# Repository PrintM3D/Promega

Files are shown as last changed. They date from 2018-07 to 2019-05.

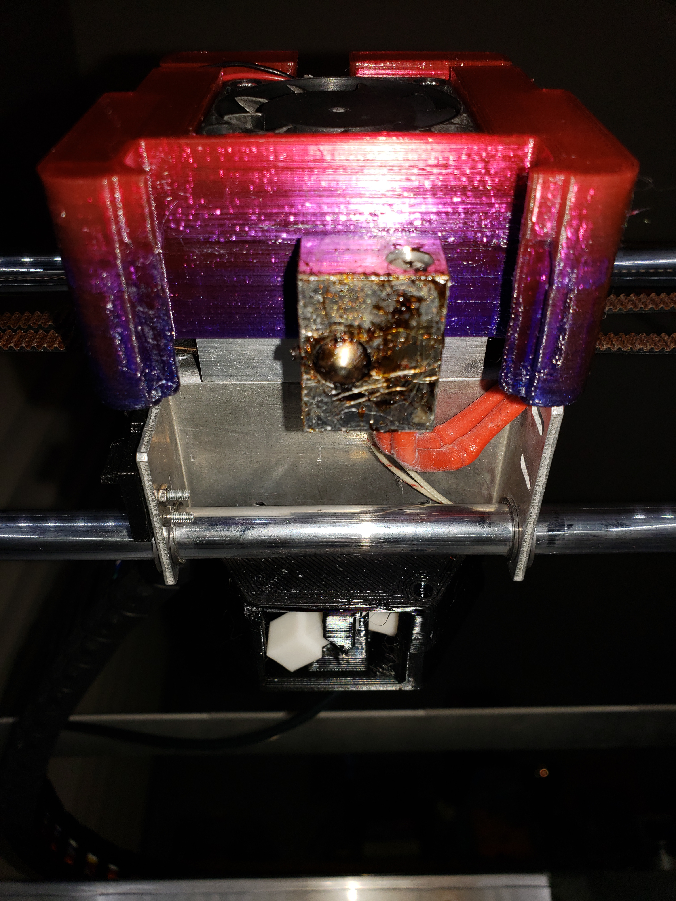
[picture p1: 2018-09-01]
addons/ShadowHawk/Fan Shroud/Photos/20180901_033425.jpg

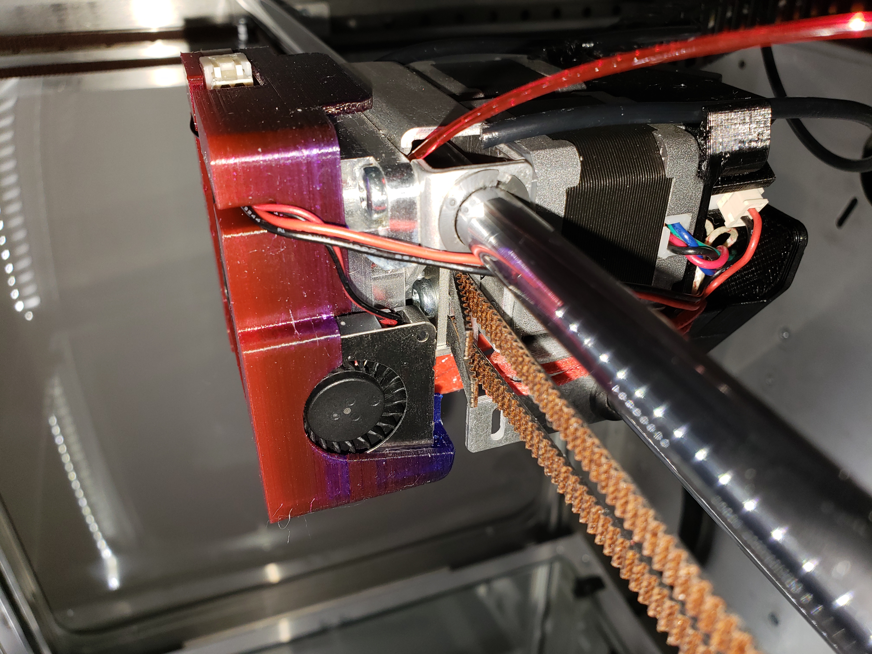
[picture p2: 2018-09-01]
addons/ShadowHawk/Fan Shroud/Photos/20180901_033406.jpg

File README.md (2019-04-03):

## Promega

> A curated repo of the official settings and files for the Promega 3D Printer.

## This Repository

* [Slicer_Profiles](https://github.com/PrintM3D/Promega/tree/devel/Slicer_Profiles) - Promega Slicer Profiles
* [SD Card Structure](https://github.com/PrintM3D/Promega/tree/devel/SD%20Card%20Structure) - Official SD folder releases

## Links
* [Promega Docs](http://promega.printm3d.com) - Official Promega Documentation. 

## Addons
* [Addons](https://github.com/PrintM3D/Promega/tree/devel/addons) - Collection of addons created by M3D and the community.

## Instructions Links:
* [How to Download SD Card Content](https://promega.printm3d.com/getting-started/updating-sd-card-structure)

## Creating Issues 
Please log ONLY issues pertinent to software bugs or operational anomalies (suspected to be software-related).
Any other type of issues logged will be not be addressed and will be deleted.

If you are looking for support, feel free to look through our ever-improving documentation for quick help. 

- [M3D's Official Troubleshooting & Self-Help Guide](https://coda.io/d/M3D-Official-Troubleshooting-Self-Help-Guide_dzE73kMbIAL/Introduction_sucuq#_lulpw)
- [Promega Guides & Instructions](https://promega.printm3d.com/)

If you'd like to voice your input on improving our documentation, visit: 
- M3D's Official Troubleshooting & Self-Help Guide [Contribution & Suggestion Page](https://coda.io/d/M3D-Official-Troubleshooting-Self-Help-Guide_dzE73kMbIAL/Coda-Edits-Requests-Form_suKF6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)
- Promega Guides & Instructions [Contribution & Suggestion Page](https://promega.printm3d.com/#contributing)

Our support ticket is available at https://store.printm3d.com/pages/support.

-M3D Team

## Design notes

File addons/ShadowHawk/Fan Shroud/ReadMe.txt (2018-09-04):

This is a 3D printable fan shroud for the ProMega using the original front and part fans.
It can also accommodate a Noctua 40x40x12 fan.

Please note, to install this fan shroud, you have to turn your heat block by 90 degrees with the wires coming out the back.  Please refer to the photos on how the cables should be routed.

The cable for the part fan needs to be removed from the front cable assembly.  You then have to pull a bit more of the cable through the cable chain (there is plenty of slack at the board end).  Refer to the photos on how the part fan cable should be routed and how the plug fits into the fan shroud.

This was modeled in Fusion 360 and I included the Fusion 360 archive file in the CAD folder together with just about any other format Fusion 360 can export.  The STL is in the folder STL (shocking).  The Simplify3D folder has a factory file in it.  The speed is set to 30mm/s, please adjust to what ever your printer is capable of printing.
The GCode folder has two files in it.  One is using Tool 0, the other one is modified to use the mixing tool with a linear gradient between the right and the left extruder.

This version now fits under the front metal edge.  You will need to adjust your Max Y in machine_axisdimension.g from 388 down to 372 due to the radius at the front of the case, BUT, you gain some cooling for your extruder steppers in return.

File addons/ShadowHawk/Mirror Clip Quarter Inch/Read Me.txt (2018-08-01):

In my setup I'm using a custom cut 16 3/8" x 16 3/8" x 1/4" mirror with half inch radius corners.
The mirror ended up being 5.99mm thick which is too thick for the regular bed clips.

I designed these clips to go between the bedframe and the heat bed and hold the mirror in place on top.
The mirror is pretty heavy as it is so this is really just a little bit of additional piece of mind.

I printed the clips in Black Inland PETG with 0.5mm nozzle, 0.25mm layer height and 30mm/s speed.

Simplify3D factory provided for convenience

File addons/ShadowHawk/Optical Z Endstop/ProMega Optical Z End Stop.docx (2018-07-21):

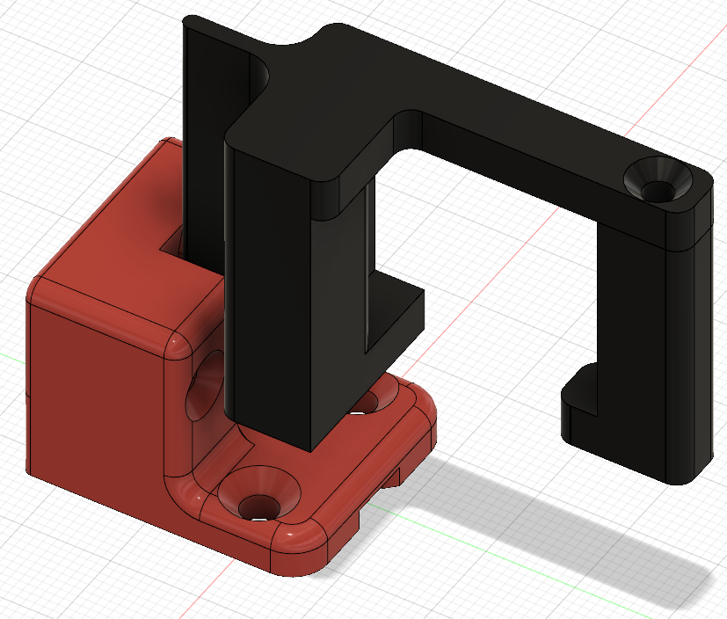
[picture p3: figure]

# ProMega Optical Z End Stop

# Introduction

In a CoreXY printer setup, the Z end stop is usually located at the bottom of the printer which equates to the maximum Z extent. Due to this, having an accurate and repeatable height measurement from that end stop to the nozzle is very important. In the existing Z end stop design, the bed rests on the actual mechanical switch and the switch is not mechanically fixed in the Z direction, i.e. it can have a little bit of play. Even if the amount of possible Z movement of the switch is only 0.5mm, that is by far too much, causing issues with repeatable Z zero position after homing the Z axis.

The Optical Z End Stop design solves those issues and yields perfect Z zero position every time.

# Bill of Materials

The following parts are needed:

- Optical Switch, here are two links, they are all the same model, just different quantities. This should give you an idea of the model used. There are other optical switches but they might not fit the 3D printed case below. https://www.amazon.com/Solu-Optical-Endstop-Printer-Makerbot/dp/B00V2QPU4M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 https://www.amazon.com/HONG111-Optical-Endstop-Control-Printer/dp/B071KBC3P8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
- 3D Printed Optical End Stop Housing Optical Z Endstop Holder.stl
- 3D Printed Slider Fin Main Fin.stl
- 3D Printed Counter Mount Counter Mount.stl
- 3 x M3 x 12mm countersunk screw
- 2 x M3 nut
- 2 x Small Cable Tie
- 1 Dupont 3 port plug (optional) https://www.amazon.com/620-PCS-2-54mm-Pitch-JST/dp/B07BCYTL7R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
- 1 M3 Threaded Brass Insert (something like the link below) https://www.amazon.com/a16041800ux0827-Cylindrical-Knurled-Threaded-Embedded/dp/B01IZ1RN0A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

# Assembly

## Optical End Stop

Make sure that the optical switch is perfectly flat against the PCB. If necessary, heat the pins up with a soldering iron and press the switch on the PCB until it is flat. Pay attention not to ruin the solder pads on the PCB.

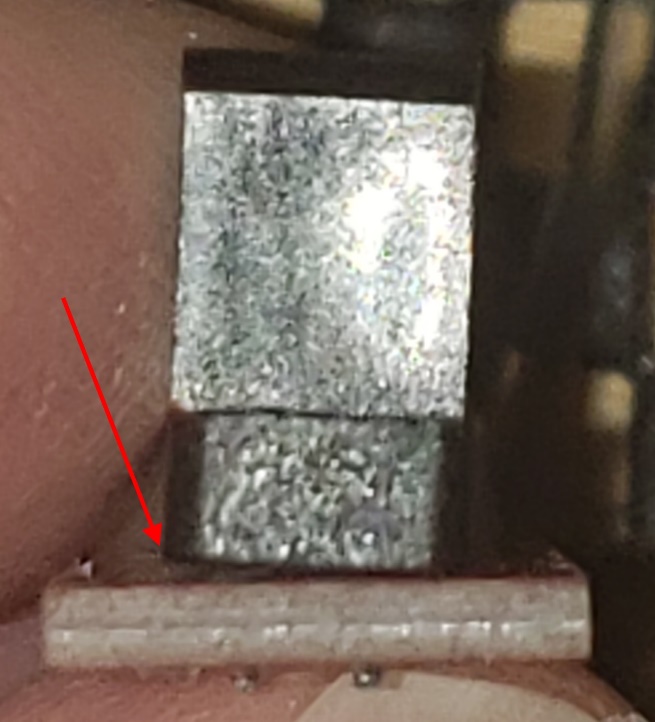
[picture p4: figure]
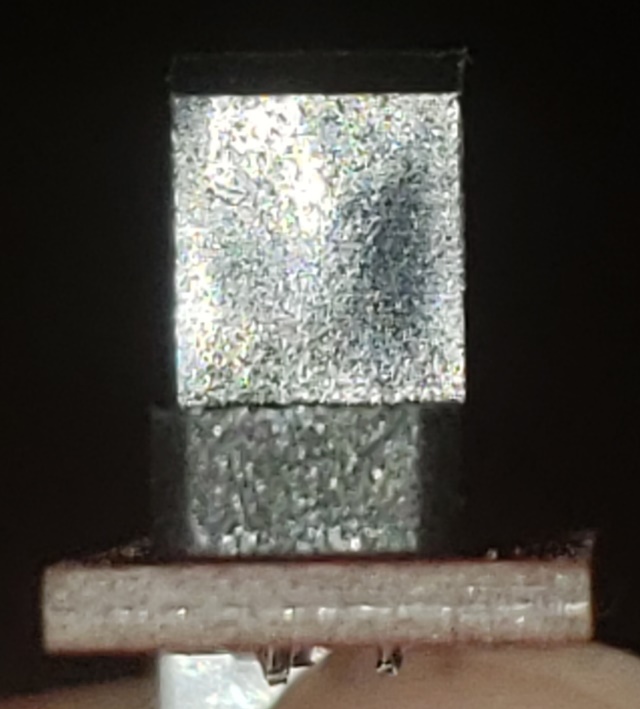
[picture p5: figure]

Once the 3D printed parts are done, insert the optical switch into the housing and fix it in place with the two screws and nuts.

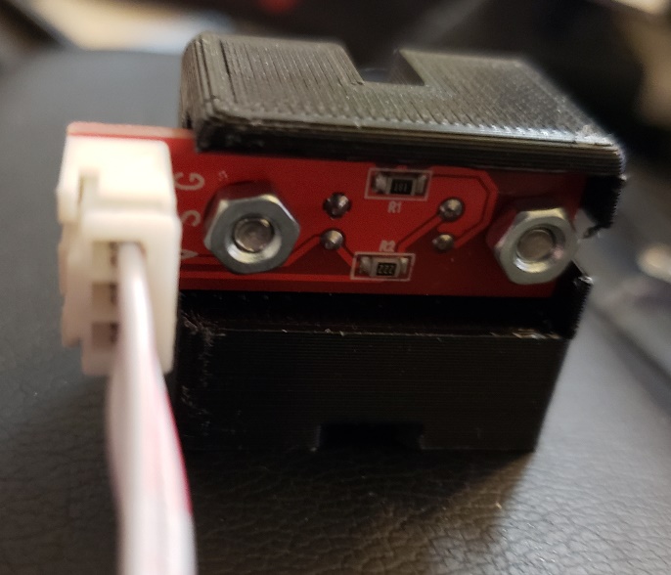
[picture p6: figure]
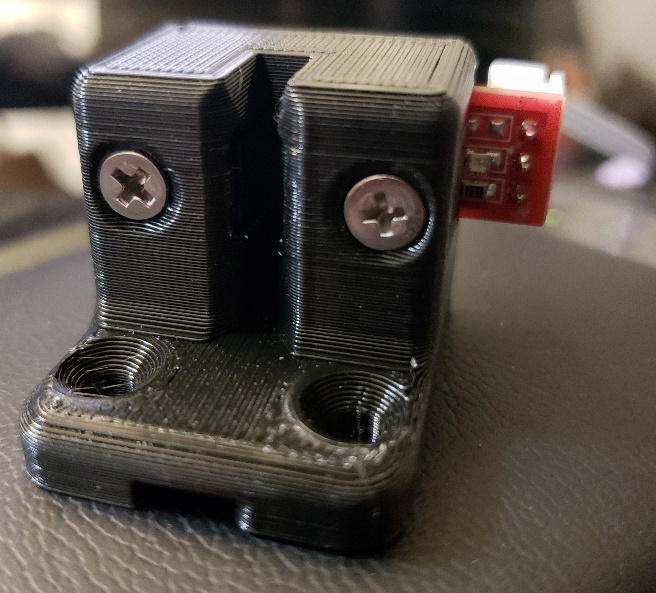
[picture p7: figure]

If you chose to get the 3 port Dupont plug, take the black single plugs off the sensor cable and put them in the correct order into the 3 port plug. Pay attention that the 3.3V and signal lines need to cross over.

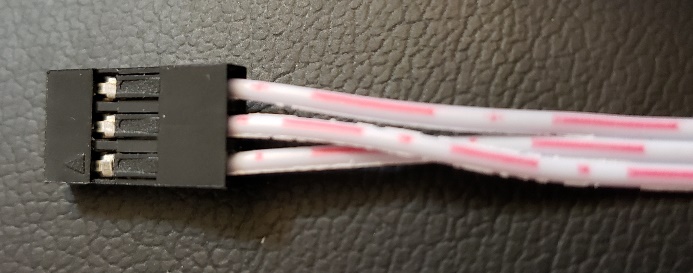
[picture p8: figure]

The order from top to bottom in the previous picture is:

1. GND
2. 3.3V
3. Signal

## Installing the Fin

Heat up your soldering iron and melt the threaded brass insert into the hole of the counter mount. Make sure that the insert is perfectly straight. Let the part cool down until no longer hot to the touch.

With the printer running, move the bed to about half way up. Slide the main fin onto the back right Z slider. Make sure it is nice and snug on it. Use the M3 screw to screw the counter mount onto the main fin so that it holds the main fin in place and the L goes along the side and underneath the Z slider.

Check that the fin is all the way pushed in and doesn’t wiggle.

## Installing the optical end stop mount

Move the bed further up to have access to the mechanical Z end stop. Remove the screws and nuts from the mechanical z end stop holder. You will need those screws and nuts in a moment.

Use a cable clipper to cut the cable tie that ties the end stop cable to the case. Also cut the cable tie holding the cables together near the board. Unplug the mechanical end stop switch from the board and put the switch and holder aside.

Take the new Z End Stop Mount, route the cable from the back through the channel under the switch and align the switch with the two holes where the old mount used to be. Insert the two screws from the original mount and tie the nuts on the back. Before you tie it all the way down, make sure once more that the cable is nicely routed through the channel under the end stop mount. Once that is verified, tie the nuts tight. Now route the cable through the same opening in the back of the case where the old cable went through and use a cable tie to fix it to the case.

Plug the Dupont plug into the plug marked in green below. If you used the 3 port Dupont plug, make sure the arrow is at the top left, if you’re using the three individual plugs, make sure you plug them onto the correct pin.

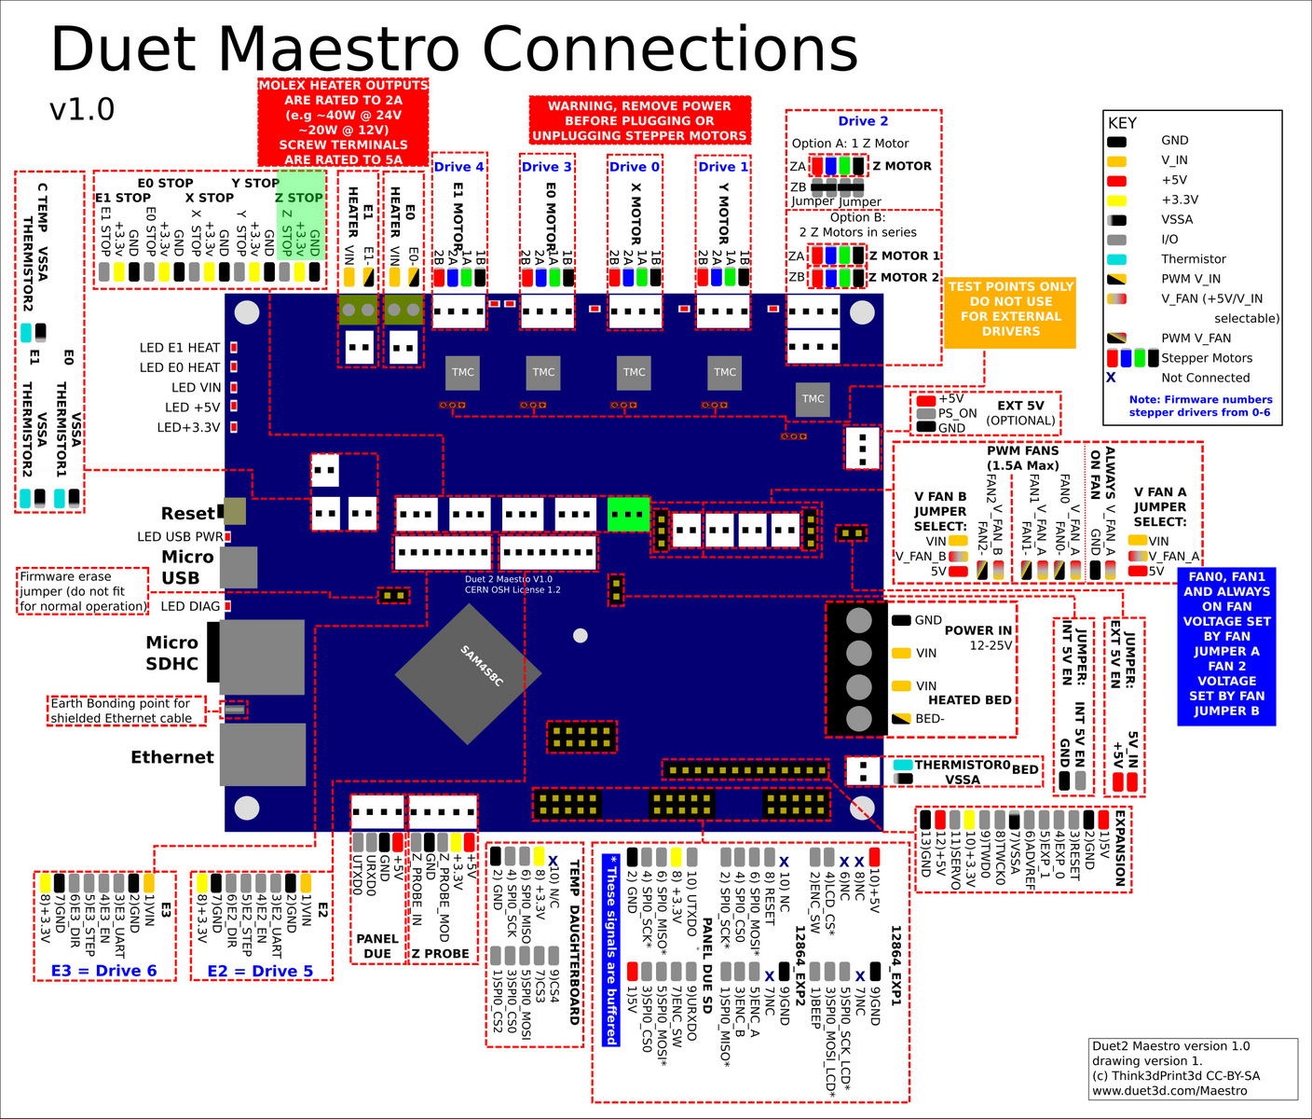
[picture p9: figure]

Use another cable tie to tie the cables at the board together like they were before you removed the mechanical switch cable.

## Software Configuration

Next, you need to change the end stop software configuration. This is done in the file machine_endstoptypes.g.

Uncomment the two M574 commands in the optical end stop section and comment the M574 command in the mechanical end stop section.

## Test proper installation

Now lower the bed gently until the fin is just above the probe. Visually check that the fin aligns with the slit in the probe and adjust the fin if necessary. When the fin looks to be in the right place, lower the bed in 1mm steps into the end stop. If that fits without scraping, you’re good to go. If it does scrape, you might want to move the bed up again, readjust the fin or possibly remove it and sand the two sides to make it smooth.

Once the fin fits nicely into the slot, lower the bed until it is about at the bottom. Then restart the printer.

Go into the Web UI, Settings Section, Machine Properties tab. You should see a ‘Yes’ under the Endstop hit column for drive 2, i.e. the Z axis. If that shows as yes, congratulations, you have wired and configured everything correctly. If it shows No, then check the software configuration and the plug once more until it does show as Yes.

You should now be able to home the Z axis. You will have to do the Z end stop calibration again as outlined in machine_zendstop.g

### Appendix A: Printing instructions

The parts were designed to be printed with a 0.5mm nozzle at 0.25mm layer height. They can be printed in PLA or PETG as they are not exposed to excessive heat.

### Appendix B: File List

- Optical Z Endstop Holder.stl
- Main Fin.stl
- Counter Mount.stl

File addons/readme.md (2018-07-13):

## This is a collection of Add-ons created by the M3D and the community 
> Please use the sample folder as a starting point

## How can I participate and contribute? 
  In order to contribute to this repo you must:
  
  * Fork this repo 
  > A fork is a copy of a repository. Forking a repository allows you to freely experiment with changes without affecting the original project. Most commonly, forks are used to either propose changes to someone else's project 
  * Create a new folder with your contribution inside Promega/addons/{Your folder}.
  * Save and commit the changes to your repo.
  * Once your changes are online, you can  perfom a pull request from your forked repo into M3D's official repo.
  * The fork will be reviwed by M3D and if approved merged into the official repository.

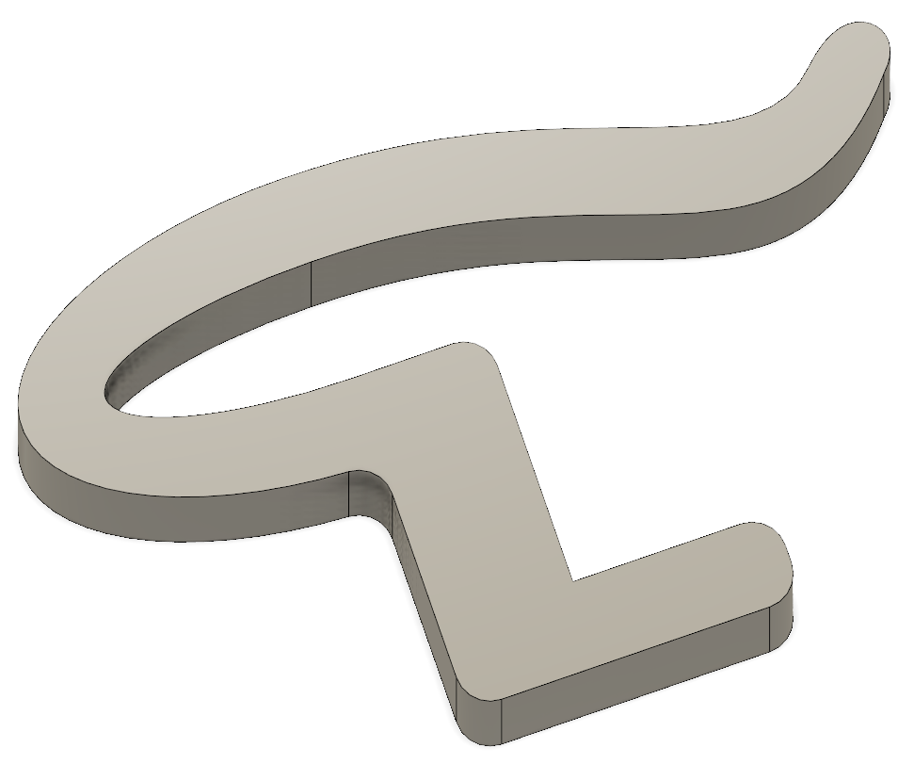
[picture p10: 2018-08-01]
addons/ShadowHawk/Mirror Clip Quarter Inch/MirrorClip.png

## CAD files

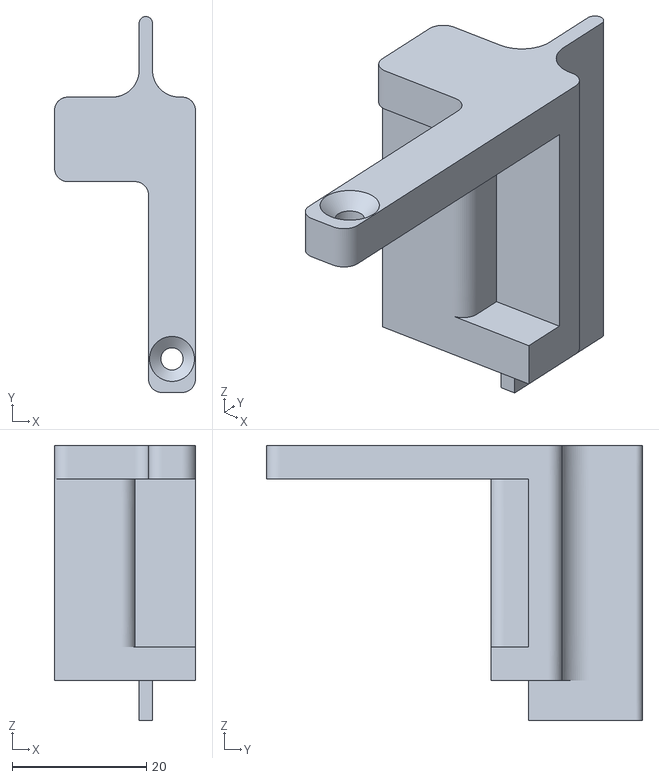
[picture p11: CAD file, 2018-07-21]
addons/ShadowHawk/Optical Z Endstop/Main Fin.stl
21.0 x 56.0 x 41.0

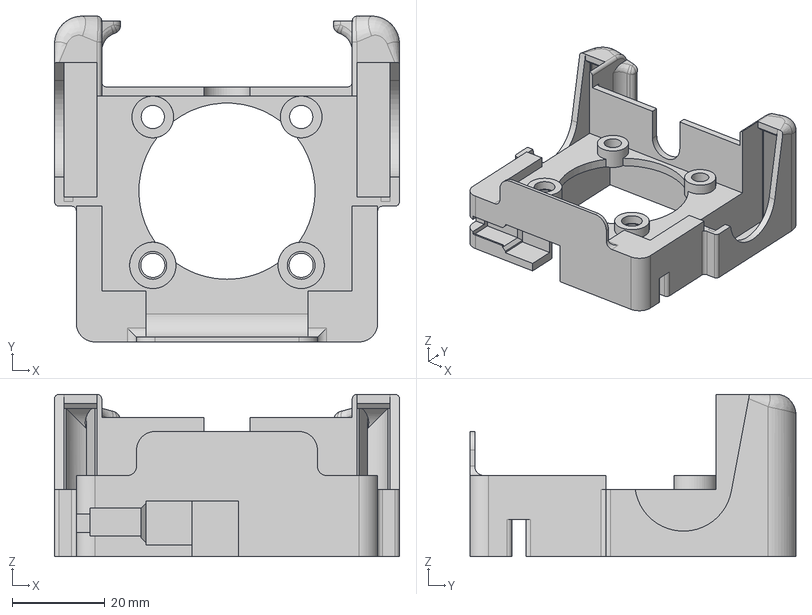
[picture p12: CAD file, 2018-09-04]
addons/ShadowHawk/Fan Shroud/CAD Files/ProMega Front Fan Shroud With Top Fin v23.step
74.4 x 70.2 x 35.0 mm

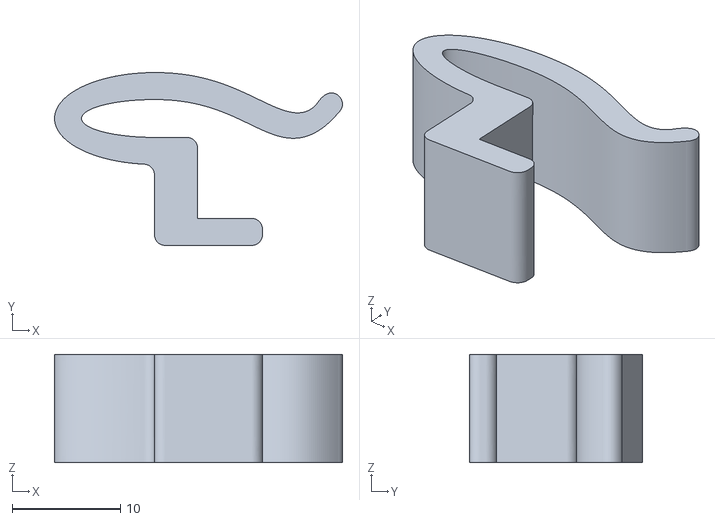
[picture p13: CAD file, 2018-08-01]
addons/ShadowHawk/Mirror Clip Quarter Inch/MirrorClip.stl
26.7 x 16.0 x 10.0

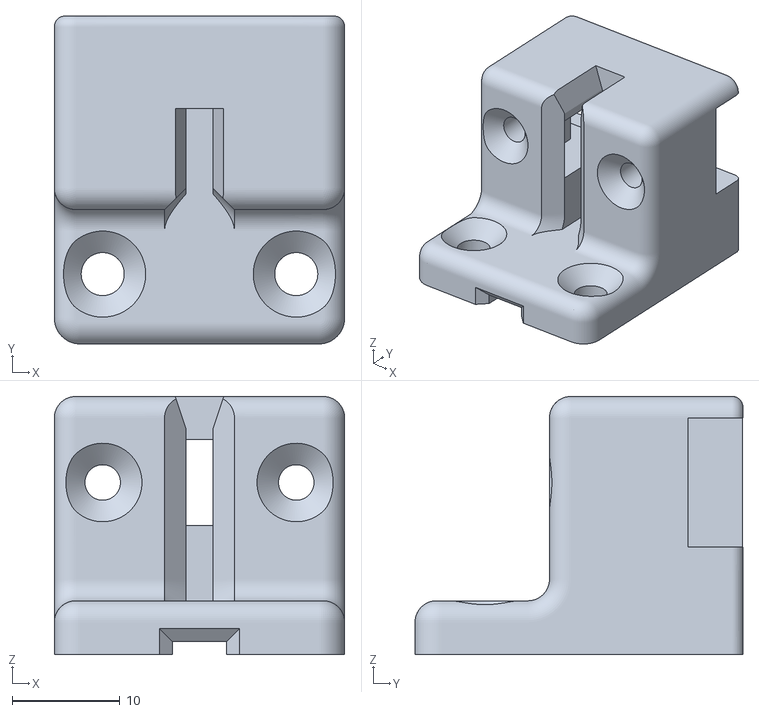
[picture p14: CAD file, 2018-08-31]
addons/ShadowHawk/Optical Z Endstop/Optical_Z_Endstop_Holder_-_Rev_A.stl
27.0 x 30.5 x 24.0

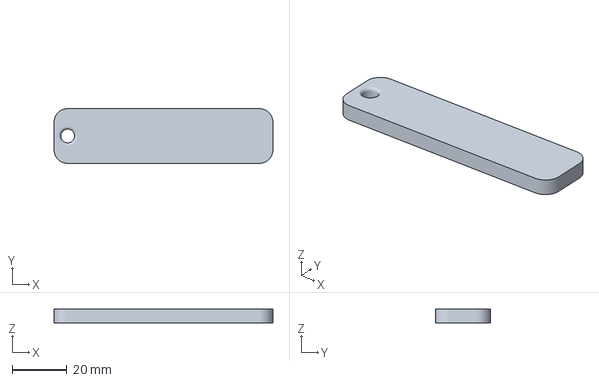
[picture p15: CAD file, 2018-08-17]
Cura Profiles/ProMega Machine Profile for both Compound and K'Tana/CFDMP_Promega_Machines.curaproject.3mf
80.0 x 20.0 x 5.00 mm

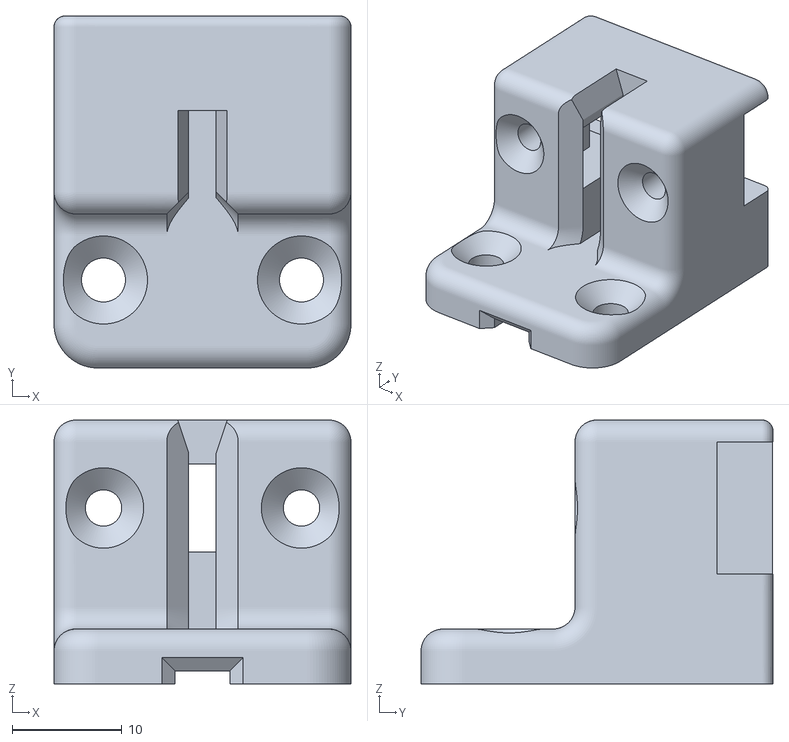
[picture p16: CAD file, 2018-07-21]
addons/ShadowHawk/Optical Z Endstop/Optical Z Endstop Holder.stl
27.0 x 32.0 x 24.0

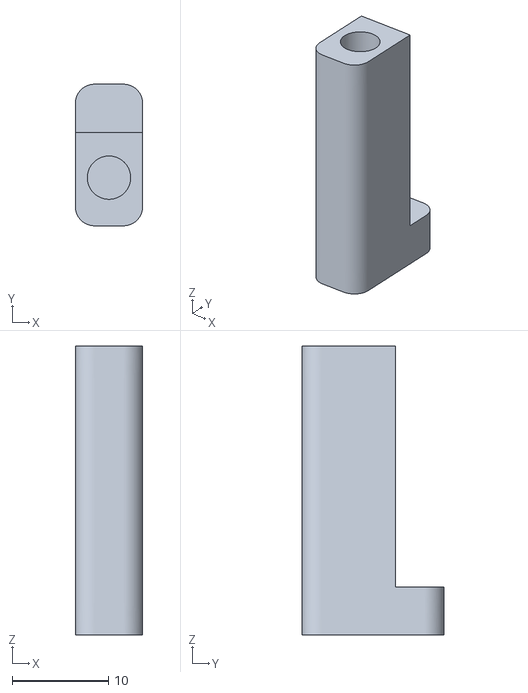
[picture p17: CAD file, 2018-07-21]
addons/ShadowHawk/Optical Z Endstop/Counter Mount.stl
7.00 x 14.7 x 30.0

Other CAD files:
addons/ShadowHawk/Fan Shroud/STL/ProMega_Front_Fan_ShadowHawk v1.7.stl
addons/ShadowHawk/Fan Shroud/CAD Files/ProMega Front Fan Shroud With Top Fin v23.f3d
addons/ShadowHawk/Fan Shroud/CAD Files/ProMega Front Fan Shroud With Top Fin v23.iges

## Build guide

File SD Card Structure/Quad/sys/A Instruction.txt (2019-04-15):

===============================================================================
====                                                                       ====
====            ProMega Machine Configuration Instructions                 ====
====                                                                       ====
====    A colaboration of: ShadowHawk, talryyn, Rodney, Lmx and others.    ====
====                                                                       ====
===============================================================================

This document explains how to set the correct configurations for this machine.

The sys folder contains a set of files, most of them should not be modified.
Some of them are machine generated, like for example the heightmap.csv file.
Here is the list of files the user can change and an overall guide on how to
configure those files. Each of those files has detailed instructions in them
under which circumstances and how that particular file has to be modified.

All the files the user should ever have to change start with the prefix machine_.
All other files can be changed, but should not be.

More in-depth guides and walkthroughs can be found on the Promega Docs website:

http://promega.printm3d.com/

== File ==			       == Description ==
A Instruction.txt         	       This document
machine_access.g         	       Handles the name of the machine as well as its IP address
machine_axisdimension.g  	       Sets the minimum and maximum extent of the three axis
machine_axissteps.g      	       Sets the step size for the three axis
machine_bedmesh.g        	       Defines the size and density of the bed mesh
machine_quad_tools.g     	       Defines the tools for the quad extruder
machine_endstoptypes.g   	       Defines the type of end stops used in the printer
machine_extruderstep.g   	       Sets the step size for the extruders
machine_maxtemp.g        	       Sets the maximum temperatures for the bed and hot ends
machine_steppercurrent.g               Sets the motor and idle currents
machine_stepperspeed.g   	       Sets the accelerations, max linear speeds and speed changes
machine_zendstop.g       	       Sets the Z height of the Z end stop
machine_zprobe.g         	       Defines the type of Z probe used and its offsets

Print Scripts:
There are two scripts in the sys folder that make starting and stopping a print more convenient.
These two scripts can be modified by the user to accommodate their personal taste of what should happen before and after a print job.

print_startcode.g        This script should be called by the slicer on start of a print job.
print_stopcode.g         This script should be called by the slicer at the end of a print job.

To call those scripts from the slicer, use the following gcode commands:
M98 Pprint_startgcode.g
M98 Pprint_stopgcode.g

Initial setup:

Step 1 needs to be done on a computer with an SD card reader and a text editor the rest will be done through macros in the Printer Setup folder.

1. Set the machine name and IP address in machine_access.g
2. Run the macro 'Printer Setup -> _1_Calibrate_Z_Probe.g'
3. Run the macro 'Printer Setup -> _2_Set_Z_Endstop_Height.g'
4. Run the macro 'Printer Setup -> _3_Mesh_Bed.g'
5. Repeat from step 3 and recheck values if necessary

At this point in time, your printer should be ready for the first test print.

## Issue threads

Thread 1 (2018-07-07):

What is the CFM on the nozzle cooling fan

PrintM3D, 2018-07-07:
Q&A test:
What is the CFM on the nozzle cooling fan

PrintM3D, 2018-07-07:
Here is the answer:
The Specs are 8000 rpm 30x30x7 mm 5V  CFM 1.65, PWM controllable, stop protection, no reverse wire polarity protection

Closed 2018-07-07.

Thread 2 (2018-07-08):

Head thermistor fault.

benburch93, 2018-07-08:
I have an issue with the connector on the head thermistor.

I was getting high readings, and re-seated cables a few times and never got it down to ambient.

Then it went to 2000 degrees and fault.

I took the back off the cable box and disconnected the thermistor an noticed that one of the male pins was pushed back and I fixed that with a pick.  But I was still getting a high reading.  Then I noticed the one of the wires into the female connector was basically floating in its socket.  It appears that it was crimped with some of the fabric and this prevented a solid connection.  When I pull back the fabric and push the bare wire in, we then read ambient, but it does not remain that way unless held in place.

I am going to attempt a temporary repair with metal foil pushed in behind the wire, but I do not expect that t last long term.

Can I please get a new thermistor sent out?

Thank you!

benburch93, 2018-07-08:
PS - tried putting this onto air table and I couldn't get it to go...

PrintM3D, 2018-07-09:
noted, removed your personal info.

daniel-farina, 2018-07-31:
Closing this issue as we are aware of it and it's currently on the Airtable. We will transition all issues to Github eventually.

Closed 2018-07-31.

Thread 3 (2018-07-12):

What is being done to fix the bed level switch so that the solder joints don't break?

daniel-farina, 2018-07-12:
This is a new issue.  Since limit switches we intended to be stationary, it seems they're being cycled beyond their design.  The initial limit switches we made were a stand in for the ones were making in the long term.  We'll reduce stress at the interface in those and the new design is also a deployable slide switch.

UPDATE 07-07-2018  Limit switches issues have been pushed to the manufacturers, who is making new ones that are soldered better;  The print file that holds them in place will then lock in the wires to eliminate bending stresses on that joint.

⚠️ _This question was originally posted on Airtable. It has been moved to Github for better trackability_

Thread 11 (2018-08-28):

part 2?

jbolene, 2018-08-28:
it is the end of August, part 2 was supposed to be posted

sohjsolwin, 2018-09-06:
I agree with this. I'm looking forward to more information included in the second half of the promega update. Will this be coming soon or is there a new estimated time frame?

ericl-m3d, 2019-04-03:
Hello,

Please log ONLY issues pertinent to software bugs or operational anomalies (suspected to be software-related).
Any other type of issues logged will be not be addressed and will be deleted.

If you are looking for support, feel free to look through our ever-improving documentation for quick help.

- [M3D's Official Troubleshooting & Self-Help Guide](https://coda.io/d/M3D-Official-Troubleshooting-Self-Help-Guide_dzE73kMbIAL/Introduction_sucuq#_lulpw)
- [Promega Guides & Instructions](https://promega.printm3d.com/)

Our support ticket is available at https://store.printm3d.com/pages/support.

If you'd like to voice your input on improving our documentation, visit:
- M3D's Official Troubleshooting & Self-Help Guide [Contribution & Suggestion Page](https://coda.io/d/M3D-Official-Troubleshooting-Self-Help-Guide_dzE73kMbIAL/Coda-Edits-Requests-Form_suKF6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)
- Promega Guides & Instructions [Contribution & Suggestion Page](https://promega.printm3d.com/#contributing)

-M3D Team

Closed 2019-04-03.

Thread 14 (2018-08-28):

quad head status

jbolene, 2018-08-28:
the kickstarter surveys were supposed to go out this week
what is the status?
when are they shipping?
are they faster than the compound?
where are the mounts?

michaelarmani, 2018-08-31:
surveys are going out as we speak.
Mounts are being internally developed / under testing currently
they are shipping over the course of the next 1-2 weeks.
They seem to be able to extrude quite a bit faster than compound, probably owing to a variety of factors.  45 mm/s  0.2mm layers 0.4mm width = 3.6mm^3/s for PLA is where we were on prototype versions which were set very conservatively.

jbolene, 2018-09-03:
I am backer #1 group #1, seems if surveys were going out that I would have one

sohjsolwin, 2018-09-06:
@jbolene are you referring to the crane quad backing on FFL, the QuadFusion print head only backing on FFL, or the QuadFusion backing on Kickstarter?

Closed 2019-04-03.

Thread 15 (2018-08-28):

machine version?

jbolene, 2018-08-28:
how are we to know which version we have to know where to start looking at the changes needed to bring it up to the current production model?

sohjsolwin, 2018-09-06:
For the software: It's best to begin by updating to the latest files available on the github when receiving your printer. From there, it's a matter of personally keeping track of what release you updated to. You could place a file on your SD card to keep track of it if you like.

For the hardware: Having some sort of internal "revision" number for the printers would be beneficial. Something that relates to the combination of the 3D printed parts plus any other modifications that come from M3D and are implemented on the assembly line.

For improvements that are suggested/made available, but are not implemented in the assembly line, simply indicating such should be sufficient for tracking. having a page in the wiki that lists the "revision" numbers, possibly with a dedicated page per revision that lists and links to each part revision would be helpful.

Closed 2019-04-03.

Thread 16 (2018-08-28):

extruders

jbolene, 2018-08-28:
https://store.printm3d.com/collections/parts/products/m3d-dual-independent-ktana-extrusion-sub-assembly-m3d0540806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

why is this part suggested for the lite machine when it does not have all the parts with it to install it?
it assumes you already have the compound installed and uses parts from it

ericl-m3d, 2019-04-03:
Hello jbolene,

Please log ONLY issues pertinent to software bugs or operational anomalies (suspected to be software-related).
Any other type of issues logged will be not be addressed and will be deleted.

If you are looking for support, feel free to look through our ever-improving documentation for quick help.

- [M3D's Official Troubleshooting & Self-Help Guide](https://coda.io/d/M3D-Official-Troubleshooting-Self-Help-Guide_dzE73kMbIAL/Introduction_sucuq#_lulpw)
- [Promega Guides & Instructions](https://promega.printm3d.com/)

Our support ticket is available at https://store.printm3d.com/pages/support.

If you'd like to voice your input on improving our documentation, visit:
- M3D's Official Troubleshooting & Self-Help Guide [Contribution & Suggestion Page](https://coda.io/d/M3D-Official-Troubleshooting-Self-Help-Guide_dzE73kMbIAL/Coda-Edits-Requests-Form_suKF6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)
- Promega Guides & Instructions [Contribution & Suggestion Page](https://promega.printm3d.com/#contributing)

-M3D Team

Closed 2019-04-03.

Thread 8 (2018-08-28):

changelog

jbolene, 2018-08-28:
Why are there no descriptions of what changed and why?
There should also be a before and after pic.
How are we to know what version we have?
Since there are no reasons for change we have no idea what the reasons are and if we need to make those changes also.

jbolene, 2018-08-28:
https://promega.printm3d.com/changelog

nothing to tell me what changed and why, no pictures, no descriptions

sohjsolwin, 2018-09-06:
Very seldom do change logs include a "why" for what was changed. Generally, they will include a link to the issue that the change resolved, at best. As more issues are included in these github repos, links like that will be possible. I agree that including some pictures or something next to the STL download files would be beneficial for users to visibly see the file. Alternatively, uploading these files to Thingiverse or a similar site that automatically generates thumbnails for them would be helpful and fulfill the same purpose.

sohjsolwin, 2018-09-06:
Linking to [Promega Docs issue](https://github.com/PrintM3D/Promega-Docs/issues/14)

ericl-m3d, 2019-04-03:
Hello,

Please log ONLY issues pertinent to software bugs or operational anomalies (suspected to be software-related).
Any other type of issues logged will be not be addressed and will be deleted.

If you are looking for support, feel free to look through our ever-improving documentation for quick help.

- [M3D's Official Troubleshooting & Self-Help Guide](https://coda.io/d/M3D-Official-Troubleshooting-Self-Help-Guide_dzE73kMbIAL/Introduction_sucuq#_lulpw)
- [Promega Guides & Instructions](https://promega.printm3d.com/)

Our support ticket is available at https://store.printm3d.com/pages/support.

If you'd like to voice your input on improving our documentation, visit:
- M3D's Official Troubleshooting & Self-Help Guide [Contribution & Suggestion Page](https://coda.io/d/M3D-Official-Troubleshooting-Self-Help-Guide_dzE73kMbIAL/Coda-Edits-Requests-Form_suKF6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)
- Promega Guides & Instructions [Contribution & Suggestion Page](https://promega.printm3d.com/#contributing)

-M3D Team

NOTE: Thank you for your suggestion and input.

Closed 2019-04-03.

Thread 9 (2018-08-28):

github changes

jbolene, 2018-08-28:
I changed the screws and tools 2 weeks ago and my changes have not appeared.
You want us to help and when we do, it seems nothing changes.

sohjsolwin, 2018-09-06:
Upon digging in, we found that you had actually closed the PR instead of leaving it open to be merged in. That is why your changes 2 weeks ago didn't go anywhere. After figuring that out and speaking with you, you managed to open the PR back up so that M3D can review and merge it in.

Closed 2019-04-03.

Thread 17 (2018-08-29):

missing screws in back heat bed

jbolene, 2018-08-29:
the back part of the heat bed wobbles if these screws are missing

the back should look like the front

jbolene, 2018-09-03:
my bed mesh was much better after adding the back screws
the back of the bed was wobbly without them
no problem if you never plan to print to the back to utilize the full bed

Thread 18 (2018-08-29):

needs to be updated

jbolene, 2018-08-29:
this is the old wiring harness not the new one

https://promega.printm3d.com/maintenance-guides/changing/changing-extruders

sohjsolwin, 2018-09-06:
For long term ease of maintenance. I would recommend linking to the "Setting up the wiring harness" page  (https://promega.printm3d.com/electrical-guides/extruder-assembly-wiring#new-extruder-assembly-wiring) for the portion that references the wiring of the exturder. This way, the assembly wiring page can be kept up for the new harnesses and such, and every page that includes a picture of the harness does not also need to be tracked and updated constantly.

Closed 2019-04-03.

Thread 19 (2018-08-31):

Plastic Insert Wear

tirelessirony, 2018-08-31:
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

In trying to track down the cause of extruder gear slipping on PLA prints I started to examine the walle and extruder gears. I had reassembled the K'tana once without the black insert, so I knew that without it 1.75 filament slides forward in the 'feed channel' and isn't pushed effectively by the extruder gear at all. I hypothesized wear on the black insert might account for play developing into skipping.

To test it, I put calipers on the black insert from my K'tana head to check the difference between the unused side and the side which had printed using ABS-R and PLA. here's the results of the thickness. The piece of plastic along the edge (the part that sits in the feed channel) tapers toward the top and is thickest where it butts up against the ptfe tube:
                             Left side (used for ~200hrs)/ Right side (nearly unused entirely)
thinnest part :      2.14mm       /   2.21mm
center             :      2.43mm      /    2.56mm
thickest part :      2.79mm      /    2.93mm

if you look at the side that has ~200hrs of use, there is a small, shiny, filament sized and shaped groove appearing (see photo). After private discussions with atleast one other user w/ 1000 hrs of use and seeing substantially more wear, I present y'all with the theory wear on the insert could be contributing to direct drive gear skipping that presents as underextrusion. Thanks for your time.

J-wMueller, 2018-08-31:
Same here, can post pictures of two different inserts with wear.

michaelarmani, 2018-08-31:
Thanks, we had planned to increase the longevity to about ~10000 hrs using nylon.

jbolene, 2018-09-03:
why not use carbon petg?  abrasiveness?
when will the new ones be available and will they be shipped to existing customers?

Turtle49, 2020-11-10:
Same happened to me. I am waiting for a Nylon insert 3D printed by a commercial printing service. Teflon/PTFE may be the best material to use, though can't be printed.

Closed 2019-04-03.

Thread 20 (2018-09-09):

The compound screws do not fit the K'tana hot end.

hallambaker, 2018-09-09:
I just took my printer apart to swap out the compound end and install a K'tana. The top two screws fit but the middle one  won't fit in the hole. A socket head screw did fit but my machine isn't all Torx screws now.

jbolene, 2018-09-09:
my ktana came with a middle screw to use

ktapper, 2018-09-09:
Could we get spec on the bolt.  I am also missing that screw

hallambaker, 2018-09-09:
I substituted an m4 sockethead which did fit. Not sure how long though.

Closed 2019-04-03.

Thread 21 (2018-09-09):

Not getting any extrusion at all.

hallambaker, 2018-09-09:
I have leveled my bed to within 1mm. I have set the end stops. I have set the temperature to 200 and loaded PLA. The tube is in the K'tana extruder.

I hit Extrude, 100 mm at 60mm/sec, nothing happens. Nothing happens at any other speed etc. either.

Also, have only one extruder showing, the other is permanently on standby.

hallambaker, 2018-09-10:
OK, have dispensed with the PTFE tubes and it is now working.

Next problem: getting PLA to stick to the bed.

sohjsolwin, 2018-11-01:
60mm/s is way too high for most filaments for an open air extrude. You will also quickly run into issue with PLA and not using the PTFE tubes. PLA does not have the necessary lubricants in the material to not burn and stick to the metal. If using the Duet Web Controller, 5-15mm/s is generally the max you want to use through that UI when testing.

ericl-m3d, 2019-04-03:
Hello hallambaker,

Please log ONLY issues pertinent to software bugs or operational anomalies (suspected to be software-related).
Any other type of issues logged will be not be addressed and will be deleted.

If you are looking for support, feel free to look through our ever-improving documentation for quick help.

- [M3D's Official Troubleshooting & Self-Help Guide](https://coda.io/d/M3D-Official-Troubleshooting-Self-Help-Guide_dzE73kMbIAL/Introduction_sucuq#_lulpw)
- [Promega Guides & Instructions](https://promega.printm3d.com/)

Our support ticket is available at https://store.printm3d.com/pages/support.

If you'd like to voice your input on improving our documentation, visit:
- M3D's Official Troubleshooting & Self-Help Guide [Contribution & Suggestion Page](https://coda.io/d/M3D-Official-Troubleshooting-Self-Help-Guide_dzE73kMbIAL/Coda-Edits-Requests-Form_suKF6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)
- Promega Guides & Instructions [Contribution & Suggestion Page](https://promega.printm3d.com/#contributing)

-M3D Team

NOTE: This [sub-section](https://coda.io/d/M3D-Official-Troubleshooting-Self-Help-Guide_dzE73kMbIAL/Promega-Troubleshooting_suSw-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) (within the Troubleshooting & Self-Help Guide) should start you off in the right direction, before submitting a support ticket (if needed).

Closed 2019-04-03.

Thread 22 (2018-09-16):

Not getting sufficient filament put down.

hallambaker, 2018-09-16:
I am getting really bad extrusion. The filament does not seem to be coming out in sufficient quantity. I have reduced the feed rate to 30mm/sec for infill, 15mm for walls.

Seems that the issue is either a blocked nozzle or the motor isn't able to pull the filament. the spool seems to jerk a lot during printing like there is too much friction.

I can't get anything using the PTFE tubes and so went direct.

ericl-m3d, 2019-04-03:
Hello hallambaker,

Please log ONLY issues pertinent to software bugs or operational anomalies (suspected to be software-related).
Any other type of issues logged will be not be addressed and will be deleted.

If you are looking for support, feel free to look through our ever-improving documentation for quick help.

- [M3D's Official Troubleshooting & Self-Help Guide](https://coda.io/d/M3D-Official-Troubleshooting-Self-Help-Guide_dzE73kMbIAL/Introduction_sucuq#_lulpw)
- [Promega Guides & Instructions](https://promega.printm3d.com/)

Our support ticket is available at https://store.printm3d.com/pages/support.

If you'd like to voice your input on improving our documentation, visit:
- M3D's Official Troubleshooting & Self-Help Guide [Contribution & Suggestion Page](https://coda.io/d/M3D-Official-Troubleshooting-Self-Help-Guide_dzE73kMbIAL/Coda-Edits-Requests-Form_suKF6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)
- Promega Guides & Instructions [Contribution & Suggestion Page](https://promega.printm3d.com/#contributing)

-M3D Team

NOTE: This [sub-section](https://coda.io/d/M3D-Official-Troubleshooting-Self-Help-Guide_dzE73kMbIAL/Promega-Troubleshooting_suSw-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) (within the Troubleshooting & Self-Help Guide) should start you off in the right direction, before submitting a support ticket (if needed).

Closed 2019-04-03.

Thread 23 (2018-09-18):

Two parts laying on floor of printer when unboxed

jackmartintx, 2018-09-18:
When the printer was unboxed there was a screw and what looks like a cable guide- black elbow - used on other corners - on the bottom.  I'm not quite sure where they go or if they are just "extra".  The bed is also titlted down to the back left corner.

jackmartintx, 2018-09-18:
Sometimes you just have to write it for the lightbulb to go off.  This is a guide for the back left cable "mast".  It is broken.  I believe that it snaps in place.  The back "snap in" is broken off.  I am basing this on the same part just below the print bed.  on basing this on the fact that the front mast has two of these sliders.  The back only the one.  I can tell from the other three that this one is broken.

1.  How do I get a new one?
2.  Do I stop all assembly and later operation until I have this replaced.
3.  I have not figured out where the screw goes.
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

ericl-m3d, 2019-04-03:
Hello jackmartintx,

Please log ONLY issues pertinent to software bugs or operational anomalies (suspected to be software-related).
Any other type of issues logged will be not be addressed and will be deleted.

If you are looking for support, feel free to look through our ever-improving documentation for quick help.

- [M3D's Official Troubleshooting & Self-Help Guide](https://coda.io/d/M3D-Official-Troubleshooting-Self-Help-Guide_dzE73kMbIAL/Introduction_sucuq#_lulpw)
- [Promega Guides & Instructions](https://promega.printm3d.com/)

Our support ticket is available at https://store.printm3d.com/pages/support.

If you'd like to voice your input on improving our documentation, visit:
- M3D's Official Troubleshooting & Self-Help Guide [Contribution & Suggestion Page](https://coda.io/d/M3D-Official-Troubleshooting-Self-Help-Guide_dzE73kMbIAL/Coda-Edits-Requests-Form_suKF6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)
- Promega Guides & Instructions [Contribution & Suggestion Page](https://promega.printm3d.com/#contributing)

-M3D Team

NOTE: This [sub-section](https://promega.printm3d.com/repair-and-maintenance/install-uninstall/slider) (within Promega Guide & Instructions) should help with installation.

This [sub-section](https://coda.io/d/M3D-Official-Troubleshooting-Self-Help-Guide_dzE73kMbIAL/All-Printable-STL-Files_sugSV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) (within M3D's Troubleshooting & Self Help) house the printed parts STL files.

Closed 2019-04-03.

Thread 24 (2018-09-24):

Extrusion problem

emilalzamora, 2018-09-24:
Hi. I have a promega.  Started working with it in early August.  Did an update etc and have had varying degrees of success. My problem is that often the extruded seems to not be able to put out enough and so I get stringy thin went sections.  Often the print will fail because that section isn’t strong. It’s a compound nozzle.
Please advise!! Thank you.
Emil Alzamora

ericl-m3d, 2019-04-03:
Hello emilalzamora,

Please log ONLY issues pertinent to software bugs or operational anomalies (suspected to be software-related).
Any other type of issues logged will be not be addressed and will be deleted.

If you are looking for support, feel free to look through our ever-improving documentation for quick help.

- [M3D's Official Troubleshooting & Self-Help Guide](https://coda.io/d/M3D-Official-Troubleshooting-Self-Help-Guide_dzE73kMbIAL/Introduction_sucuq#_lulpw)
- [Promega Guides & Instructions](https://promega.printm3d.com/)

Our support ticket is available at https://store.printm3d.com/pages/support.

If you'd like to voice your input on improving our documentation, visit:
- M3D's Official Troubleshooting & Self-Help Guide [Contribution & Suggestion Page](https://coda.io/d/M3D-Official-Troubleshooting-Self-Help-Guide_dzE73kMbIAL/Coda-Edits-Requests-Form_suKF6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)
- Promega Guides & Instructions [Contribution & Suggestion Page](https://promega.printm3d.com/#contributing)

-M3D Team

NOTE: This [sub-section](https://coda.io/d/M3D-Official-Troubleshooting-Self-Help-Guide_dzE73kMbIAL/Promega-Troubleshooting_suSw-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) (within the Troubleshooting & Self-Help Guide) should start you off in the right direction, before submitting a support ticket (if needed).

Closed 2019-04-03.

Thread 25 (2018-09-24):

K'Tana Print issues

caschles, 2018-09-24:
Team, I have installed the K'tana print head on the ProMega. The card supplied with the printer was lost and we downloaded the recent files from GitHub. The left side of the extruder works without issue. the right side heats, but will not extrude. when i look at the extruder in the Web view, everything appears to be correct.

ericl-m3d, 2019-04-03:
Hello cashles,

Please log ONLY issues pertinent to software bugs or operational anomalies (suspected to be software-related).
Any other type of issues logged will be not be addressed and will be deleted.

If you are looking for support, feel free to look through our ever-improving documentation for quick help.

- [M3D's Official Troubleshooting & Self-Help Guide](https://coda.io/d/M3D-Official-Troubleshooting-Self-Help-Guide_dzE73kMbIAL/Introduction_sucuq#_lulpw)
- [Promega Guides & Instructions](https://promega.printm3d.com/)

Our support ticket is available at https://store.printm3d.com/pages/support.

If you'd like to voice your input on improving our documentation, visit:
- M3D's Official Troubleshooting & Self-Help Guide [Contribution & Suggestion Page](https://coda.io/d/M3D-Official-Troubleshooting-Self-Help-Guide_dzE73kMbIAL/Coda-Edits-Requests-Form_suKF6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)
- Promega Guides & Instructions [Contribution & Suggestion Page](https://promega.printm3d.com/#contributing)

-M3D Team

NOTE: This link (within Promega Guides & Instructions) may help: https://promega.printm3d.com/advanced-setup-guides/meet-the-extruder#tools

Closed 2019-04-03.

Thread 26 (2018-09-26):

K'Tana severe Skipping

ANataleIII, 2018-09-26:
I am unable to get any successful prints with PLA or PETG. The skipping from the extruder is terrible. Ive made all the adjustments suggested, updated firmware, I drilled out the sleeve, but the skipping continues to grow. Now I cant even extrude the filament to purge without severe skipping and prints fail. I have tried temps from 195 to 270 depending on filament, I have tried speeds as slow as 15mm/s to 45mm/s. Ive adjusted stepper current to 550/ 550. Ive moved away from the feeder tube and run direct. Nothing is working. Link to the video is below. The fan was disconnected for the video but is normally running. the skipping is the same either way.

https://youtu.be/eBqOyhDG8G4

ericl-m3d, 2019-04-03:
Hello ANatalelll,

Please log ONLY issues pertinent to software bugs or operational anomalies (suspected to be software-related).
Any other type of issues logged will be not be addressed and will be deleted.

If you are looking for support, feel free to look through our ever-improving documentation for quick help.

- [M3D's Official Troubleshooting & Self-Help Guide](https://coda.io/d/M3D-Official-Troubleshooting-Self-Help-Guide_dzE73kMbIAL/Introduction_sucuq#_lulpw)
- [Promega Guides & Instructions](https://promega.printm3d.com/)

Our support ticket is available at https://store.printm3d.com/pages/support.

If you'd like to voice your input on improving our documentation, visit:
- M3D's Official Troubleshooting & Self-Help Guide [Contribution & Suggestion Page](https://coda.io/d/M3D-Official-Troubleshooting-Self-Help-Guide_dzE73kMbIAL/Coda-Edits-Requests-Form_suKF6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)
- Promega Guides & Instructions [Contribution & Suggestion Page](https://promega.printm3d.com/#contributing)

-M3D Team

NOTE: The troubleshooting guide should be able to set you in the right direction, before sending a ticket (if needed).

Closed 2019-04-03.

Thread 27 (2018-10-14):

Pro mega Network Setup

WilliamLalum, 2018-10-14:
We are unable to get either of our laptops to connect to the pro mega.  We have changed none of the default settings on the sd card.
We have an Ethernet cable attached to the printer to our router.  Lights come on as instructed.  Power is on to the duet board.  When we open a browser in chrome with the address of promega/ we get a IP address cannot be found. Any advice?

WilliamLalum, 2018-10-14:
Ok. We found the IP address the router is assigning to the printer. Should we set the M552 command to that address on the SD card?

sohjsolwin, 2018-11-01:
> The instructions assume that your router has a built-in LAN DNS for devices that use DHCP to get their IP addresses. It's a bad assumption because most low cost routers don't.

I disagree with that statement. Every _router_ I've ever owned, even the cheap ones, have assigned IP addressed to devices connected to them. _switches_ on the other hand, just pass the connection along and do not assign IPs.

> Ok. We found the IP address the router is assigning to the printer. Should we set the M552 command to that address on the SD card?

No, you do not need to set the IP in the SD card, unless you want to use a static IP. If that is the case, you should also make it static on your router so that on a renew it does not potentially assign that same IP to something else on your network first. If you do not assign a static IP, you should be able to access the printer from http://promega/ regardless of which IP the router ends up assigning to it.

TheBum, 2018-11-01:
I’m referring to the instructions that say to type “promega” into the address field in the browser. That doesn’t work on most home routers.

ericl-m3d, 2019-04-03:
Please log ONLY issues pertinent to software bugs or operational anomalies (suspected to be software-related). Any other type of issues logged will be not be addressed and will be deleted.

If you are looking for support, feel free to look through our ever-improving documentation for quick help.

- https://coda.io/d/M3D-Official-Troubleshooting-Self-Help-Guide_dzE73kMbIAL/Introduction_sucuq#_lulpw
- https://promega.printm3d.com/

Our support ticket is available at https://store.printm3d.com/pages/support.

-M3D Team

Closed 2019-04-03.

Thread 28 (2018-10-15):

Promega networking dead

mtkgrafix, 2018-10-15:
Just received my Promega and have tried the default SD card config with no success.

The network activity lights never show any activity (or light). I have tried multiple ETH cables (new and tested on other equipment). Tried multiple ports on the switch (also confirmed working with other equipment).

I then tried to assign a static address but that didn't help (I have the second SD card so edited that one). I've also downloaded a new SD structure for my K'tana config and nothing changed.

I have never inserted/removed the SD card with the power on. The three LEDs on the Duet board itself do light up but never see even a flash on the ETH port activity lights. It never asks my DHCP server for an IP (checked logs).

When I plug in the USB cable for the Duet the Parallels VM on my Mac does recognize the device as a 'Duet' but I'm not able to mount the SD card (either card, original or modified).

Both SD cards work just fine when inserted in the little USB converter provided. That is how I was able to edit the second card provided to try a static address.

I'm afraid the SD port is bad or there is a problem with the ETH port itself.

The Promega did arrive in good shape. I opted for the wooden crate 'just in case' packaging and the cardboard outside of that wooden crate even looked like it'd had an uneventful trip.

This image show's the only LEDs that light up when the Duet is powered up. They light up like this on the Duet and stay that way (never any on the ETH port):

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

mtkgrafix, 2018-10-15:
> Hey, log a support ticket on their site. I had a board with that issue too and had it replaced under warranty.

Thanks bass4aj - I just got my instructions to ship the board back.  👍🏻

Closed 2018-10-30.

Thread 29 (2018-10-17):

Sensor on compound head shows 25 degrees cold offset

sanslos, 2018-10-17:
The idle (cold) temperature on the Compound head shows around 0C.  It heats and cools, but starts and stops around 0C.
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

sohjsolwin, 2018-11-01:
what version of the duet firmware are you on? Have you updated it from what the printer originally shipped with? There was a change in one of the beta versions that modified the temperature readings a bit. I believe that may be related to what you're seeing (only if you've updated the firmware though).

sanslos, 2018-11-01:
It's a little more complicated than that.  This problem (low temp on Compound) was first seen with the original firmware.  I upgraded the firmware (currently 2.02RC3), no change, re-calibrated, no change.  I have a similar problem with K'Tana, where initially both sensors read about the same (around 27C at idle), then one sensor suddenly dropped to showing about 12C at idle (no change in firmware).  Note that I suspect a firmware issue, but I put a new sensor in the Compound head and it showed 27C again.  Something weird is going on.
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

![k tana initial bringup temps](https://user-images.githubusercontent.com/43072647/47858
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
183-aa86b800-dda8-11e8-8dea-90e085757903.png)

sanslos, 2018-11-01:
(Sorry, thought this posted)  This is what the K'Tana shows when first turned on

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

sanslos, 2018-11-01:
The lower temperature is consistent, it doesn't bounce around.  T1 now always shows 12C when idle.

sohjsolwin, 2018-11-01:
definitely strange. Have you run a PID tuning yet? https://promega.printm3d.com/repair-and-maintenance/temperature-calibration

sanslos, 2018-11-01:
Yes, I have (for the Compound).  I haven't done it for the current problem, I was planning to, but that wouldn't explain why it started out with both sensors showing 27C then one suddenly dropping to 12C.

sanslos, 2018-11-06:
The problems I'm seeing are due to the sensors.  I did experiments with the four sensors (Compound, 2 from K'Tana, one replacement) and two Duet ports, I currently have two failed sensors that show low.  Note the original Compound sensor now shows -18C, they deteriorate over time:

                          Duet Port (C)
Sensor   Ohms     Left    Right
        1    1046    12.40    12.00
        2    1106    27.90    27.70
        3    926    -18.10    -18.30
        4    1107    28.00    28.00

        Note: Wire Resistance = 0.6 ohms

c-schmitz, 2019-05-03:
I can confirm similar issues. Both my sensors are off by -15°C now. In the beginning they worked normally.
This caused the head being too hot at nominal temperature.

I was able to temporarily fix that by messing with the R value in the configuration However this seems to be a general quality problem with the sensors (like so many other things)

c-schmitz, 2019-09-29:
Why was this closed?

sanslos, 2019-09-29:
The issue was with the sensors, when they were replaced the issue was fixed.  I should have closed this when that was verified (last November, 2018), it was the point of my Nov. 6, 2018 post saying "The problems I'm seeing are due to the sensors", although I may not have been clear.

Note that at the time I was also having problems with the heating, [I posted a whole series of experiments on Discord](https://discordapp.com/channels/279255051036524544/461926470776782848/509255194782072852).  Once I replace the sensors and the suspect heaters everything worked fine.

For completeness I should mention that at least once (twice?) I was not able to keep temperature, which was a Duet issue.  A hard power cycle (unplugging the printer) solved that.

Closed 2019-09-27.

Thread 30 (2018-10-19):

Grinding noises during printing....

MSI-Promega, 2018-10-19:
New user. Have my printer running, but we hear grinding and squeaking noises and I have yet to isolate their location. Perhaps from the belt guide rollers...? Has anyone been experiencing this as well?

jbolene, 2018-10-19:
yes I have the noises also

tirelessirony, 2018-10-19:
I also have heard grinding noises. I picked up some compressed air and try to blow out the front and side idler pulleys every once in awhile. I think small bits of worn belt, dust, debris can get into the spaces between the smooth bearings and cause surprisingly loud grinding.

That doesn't completely solve it, but between that and cleaning/lubricating rods and rails - I've heard less. I use PTFE lube on the rails and dry-film teflon on the rods.

bass4aj, 2018-10-19:
I have encountered squeaking and grinding from 2 places: 1. is the front
idlers/bearings. The debris from the belt gets in the bearings. I just
replaced them with GT2 Idlers since they are more protected, but others
have soaked their bearings in kerosene and re lubricated them.
2. is the PTFE tubing for the filament. If it rubs along the x-gantry long
enough, it will start to screech.

On Fri, Oct 19, 2018 at 12:32 PM tirelessirony <notifications@github.com>
wrote:

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

ericl-m3d, 2019-04-03:
Please ONLY log issues pertinent to software bugs or operational anomalies (suspected to be software-related).

Any other issues logged will be not be addressed and will be deleted.

- M3D Team

Closed 2019-04-03.

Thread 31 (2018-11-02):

EXtruders Nozzels at 2 different levels - plus bed slipping?

jackmartintx, 2018-11-02:
1.  The Promega arrived with all 4 Z sliders broken.
2.  It was a nightmare trying to figure out how to redo and twist, etc.
3.  After multiple alignment and mapping attempts, I think the issue is the bed is slipping or skipping.  Z0 seems to be "moving".  What would cause this?
4.  While attempting yet another alignment and leveling I realize that now my nozzles are at two different levels.
5.  I have put close to 100 hours into the Promega and yet to print anything.

Ideas?

ericl-m3d, 2019-04-03:
Please ONLY log issues pertinent to software bugs or operational anomalies (suspected to be software-related)
Any other issues logged will be not be addresed and will be deleted.

- M3D Team

Closed 2019-04-03.

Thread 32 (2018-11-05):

Extruder Skips Then Stops

DesignSteinStudios, 2018-11-05:
I have tried using the Compound and Single K'Tana head and also ABS and PLA and I am having the same issue with the right side extruder. Everything works fine for the fist 200-300mm of a print then I can start the hear the right gear that pulls the filament into the extruder start to skip. Shortly after the gear spins so many times it carves a groove in the filament and it won't extruded anymore and I have to cancel the print.

I have taken apart the head multiple times and there are no obstructions, just the gear that has filament shavings on it and a stuck filament.

I have adjusted the nozzle temperature and feed rate and the same problem still happens. Under machine control I extrude 100mm at 5mm/sec and the first 2 rounds goes well. Then by the 3rd round it starts to skip and gets stuck. If I try to extrude at anything faster than 5mm/sec it skips constantly.

I checked my e-motor steps and there were at E1560:1532:420:420 so I typed the G code M92 E195:191.5 in and it seems to fix the readout issue but the same problem still happens.

Any ideas?

DesignSteinStudios, 2019-04-03:
So you don’t even bother to answer my question and you close it out? Your printer is a piece of fucking shit and so is your support. I will do everything possible to notify the design and maker community how horrible your printers are. I’ve already convinced 10 people from github to not purchase the Promega.

Jesse Clemmer
PRESIDENT
O – 714.375.4846 C – 949.275.4554
7602 Talbert #D, Huntington Beach, CA 92648
www.DesignSteinStudios.com<http://designsteinstudios.com/>
[logo_signature]

Confidentiality: The information contained in this e-mail transmission is intended only for the use of the individual or entity named above. This e-mail transmission, and any documents, files, previous e-mail transmissions or other information attached to it, may contain confidential information that is legally privileged. If you are not the intended recipient of this e-mail message, or the employee or agent responsible for delivering it to the intended recipient, you are hereby notified that any disclosure, dissemination, distribution, copying or other use of this transmission or any of the information contained in or attached to it is strictly prohibited. If you have received this e-mail transmission in error, please immediately notify us by return e-mail transmission or by telephone at (949) 275-4554, and destroy the original e-mail transmission and its attachments without reading, saving, or utilizing it in any manner.

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

ericl-m3d, 2019-04-03:
We understand your frustration with the delay and are doing our best to help, however we cannot tolerate profanity in our channels of communication. Please keep the language professional or we will have to stop this interaction.

ONLY logged issues pertinent to software bugs or operational anomalies (suspected to be software-related)
Any other type of issues logged will be not be addressed and will be deleted.

If you are looking for support, feel free to look through our ever-improving documentation for quick help.

- https://coda.io/d/M3D-Official-Troubleshooting-Self-Help-Guide_dzE73kMbIAL/Introduction_sucuq#_lulpw
- https://promega.printm3d.com/

Our support ticket is available at https://store.printm3d.com/pages/support

-M3D Team

DesignSteinStudios, 2019-04-03:
Horrible product, horrible design, horrible rip off. I will spread the word

Jesse Clemmer
PRESIDENT
O – 714.375.4846 C – 949.275.4554
7602 Talbert #D, Huntington Beach, CA 92648
www.DesignSteinStudios.com<http://designsteinstudios.com/>
[logo_signature]

Confidentiality: The information contained in this e-mail transmission is intended only for the use of the individual or entity named above. This e-mail transmission, and any documents, files, previous e-mail transmissions or other information attached to it, may contain confidential information that is legally privileged. If you are not the intended recipient of this e-mail message, or the employee or agent responsible for delivering it to the intended recipient, you are hereby notified that any disclosure, dissemination, distribution, copying or other use of this transmission or any of the information contained in or attached to it is strictly prohibited. If you have received this e-mail transmission in error, please immediately notify us by return e-mail transmission or by telephone at (949) 275-4554, and destroy the original e-mail transmission and its attachments without reading, saving, or utilizing it in any manner.

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

Closed 2019-04-03.

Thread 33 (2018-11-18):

Print Cooling Fans Popped and Smoked

talonzme, 2018-11-18:
Anyone know the specs on the print cooling fans (2 little ones inside shroud)?  I was running a print yesterday and they popped then started smoking (badly).  I had to unplug them.  They won't run now,obviously, so I will need to replace them.  Not sure is the printer warranty is still in effect or not.  No changing of wires was done since the voltages are different between these and the nozzle fan.  I cannot find specs to replace the two print cooling fans though.

TheBum, 2018-11-18:
Since both blew out at the same time, I would suspect the Maestro board. In any case, it absolutely should be covered by the warranty.

talonzme, 2018-11-19:
How do I start the process to get them replaced? I am not seeing any other place to submit an issue but here....

jbolene, 2018-11-19:
https://store.printm3d.com/pages/support

talonzme, 2018-11-19:
Thank you jbolene. I realized I didn't have an account for that page. I have submitted the "chat" to request the fans.

Closed 2019-01-02.

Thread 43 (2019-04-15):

Possible microstepping error.

ericl-m3d, 2019-04-15:
In machine_axissteps.g, the M350 line does not refer to the x, y, or z axis, only the e motors.

E motors microstepping is handled in machine_extruderstep.g.

Sample from machine_axissteps.g:

```
M350 E16		; Confirming default 1/16 microstepping mode for calculation, in case firmware default changes

M92 X79.8 Y79.8 Z282.6961 ; Set axis steps/mm

M350 X32 Y32 Z32          ; Setting microstepping to 1/32.
```

ericl-m3d, 2019-04-15:
Reviewing file history, might have been unintentionally added. Switched it to refer to the x, y, and z axis only

e5de959  (K'tana)
81310ca  (Compound)

Re-open if there are any objections.

Closed 2019-04-15.

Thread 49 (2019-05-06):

1st Macros bug

ericl-m3d, 2019-05-06:
There is minimal space to retract the probe.

Closed 2019-09-27.

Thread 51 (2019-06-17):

I have no idea how to use this Promega

obeydesign, 2019-06-17:
BUT I actually got it to commune with my network. However, if I understand the machine at all (not saying I do) the two feeder tubes that go through the plastic chain are not attached to anything. To what should they be inserted into.

ALSO there is a gray piece at the back of the extruder (just out of the box). Is this something to be removed? It has a few screws, and maybe THAT'S where I'm supposed to insert the filament feeding tubes? Maybe?

I'd appreciate any help. I find the online manual to be nearly worthless, especially since the included pictures are so small.

TheBum, 2019-06-17:
That piece at the back of the extruder is what corrals the connections in the head. It needs to stay in place.

TheBum, 2019-06-17:
As for feeding the filament, a lot of people don’t use those feed tubes because they provide an unnatural sharp turn into the extruders. Not using them does require that the top window on the printer be left off.

If you take a flashlight and look down into the gaps in the top of the extruder, you can see the gear that grabs the filament. Insert the filament into that path with the nozzle heated up and issue extrude commands through the web interface to feed it in.

obeydesign, 2019-06-17:
Hey, thanks for writing back. I greatly appreciate it. I'll see if I can find the gaps you're referring to. Also, did you get a piece of glass to fit on the print bed? I got four large pieces of plastic, obviously for the top and sides, but I don't think I can use plastic as the print bed.

obeydesign, 2019-06-17:
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

This is the top of my extruder. Isn't it?

TheBum, 2019-06-17:
I’ve circled the filament entry locations.

https://www.dropbox.com/s/891w4ugq1dmihe9/IMG_0272.jpg?dl=0

obeydesign, 2019-06-17:
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
Thanks! Does this look correct? I've fed it down as far as it will go. Does that mean...it's in?

TheBum, 2019-06-17:
Farther forward. The filament needs to go in front of the plate that the last few threads of the screw is going through.

obeydesign, 2019-06-17:
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
Like this?

TheBum, 2019-06-17:
That’s the right hole, but I can’t really see the angle. What happens when you try extruding? Make sure you heat up the nozzle first.

obeydesign, 2019-06-17:
Oh, I gotta be honest, I'm waiting for a flurry of answers to many other questions from M3D. I've been using Octoprint, and this whole Duet board is all new to me.

Thank you again for your time. I greatly appreciate it.

obeydesign, 2019-06-18:
Okay. I got the filaments inserted. The extruder works so far. I even went out and got a $10 piece of class to fit over the heated bed. NOW I can't get the bed to Z-height adjust. I use the instructions, but...well, like I said, no joy.

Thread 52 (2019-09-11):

bed leveling

tmaj9447, 2019-09-11:
when i run the bed mesh it seems to slam into the right side of the frame every time. the front back and left sides seem to be okay. please advise what i need to do, i was trying to find a sock promega compound sd card configuration that is original. Thanks!

michaelarmani, 2019-09-27:
See https://github.com/PrintM3D/Promega/tree/devel/SD%20Card%20Structure/Compound

Closed 2019-09-27.

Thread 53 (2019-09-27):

Tuning home position: Z-0.5 is maximum

wattronix, 2019-09-27:
I am trying to set Z home for the first time.
As I instruct the bed rise 0.5mm at a step using the Machine Control of DWC, once I try to go from Z-0.5 to Z-0.55 or Z-0.6, the head refuses to go up such that I can slowly find the level where the nozzle touches the glass plate.

Suggestions as to how to overcome are welcomed.

michaelarmani, 2019-09-27:
There is a small amount of backlash due to tension in the belts and gravity that has to be considered.  In a fine tuned system, the belts are all tight, the pulleys are checked that they are flat on the shaft and tightened,  the Z sliders on the rails are lubricated and smooth to give low friction, and extra weight is added to the bed such as thick glass to ensure gravity helps absorb backlash.  Even in such a system there will be no less than Z = 0.10mm backlash.  Please identify your backlash (it could be in the range 0.1-0.3mm usually).  From here, use this when doing calibrations, or Z-hop during prints.

wattronix, 2019-09-28:
Hello Michael,

Thank you for the response. I measured the shortfall with some feeler gauges and inputted the value.

I moved on to Set up the bed probe and assumed that the statement “Engage bed probe” was the title of the photo below. It was an in reality a not well placed instruction to lower the bed probe.
Not knowing what the G30 referred to, the bed forced its way into the nozzle and jumped down about 10mm.

Realizing the error, I homed the bed and restarted. Going thru the correct procedure with the probe lowered when required, the bed now stops quite far (~5mm) away from contacting the nozzle.
The bed Z position comes as high as Z-0.5 and will not rise further when I activate the Move Z buttons, as instructions dictate, to move the bed up to contact the nozzle. I should be having a reading for Z at this step to about -7.0.

Hoping you can guide me further.

Ron

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

michaelarmani, 2019-09-29:
You are correct, Engage probe was meant to indicate the user manually deploys the probe.

By hitting the nozzle, you've got the machine thinking it is inside the nozzle, then when it fell back ~10mm it thinks it is way off course - there is a "software endstop" that protects the nozzle from Crashing into the bed once calibrated.

To bypass this, try your procedure again but first put in this gcode command into the web interface:  M564 S0 H0, or you should be able to restart the printer (power cycle the blue-lighted switch for about 5 seconds off then on).

At the stage you are at I think you would be best served looking at the Duet documentation and talking amongst the other users in the discord or with our tech support team as the Github should be used to improve the code set if there is a systemic issue.    Please visit https://discord.gg/eQ5wPwk for the community or http://support.printm3d.com/

wattronix, 2019-10-09:
Oct8/19 (9pm)
Hello Michael,

Taking your recommendation, I took my Cura question to discord on Sept. 29
- No response from anyone to the "wattronix" posting to date.
*********************************************************************

Pressing on, I ignored the need to input values per the Promega instruction sheets, and
managed to get one side of the compound extruder to print a small object.The other side
of the extruder did not work so well.

I wrote to M#D support on Oct 6 and am still waiting anxiously. I wrote:
 "I was able to print my first model today using the right hand extruder.
The left extruder will not retract or extrude.
Motor 1 & 2 appear to be wired correctly to the DUET board.

With wiring as received, "Mixing as single Left"- No retract, no extrude. Will not print.
"Mixing as single Right"- Retract OK,  Extrude OK. Prints fine.

When motor connectors are reversed on Duet board,
"Mixing as single Left"- retract is reversed, extrude is reversed and
filament loads ~1" and then skips at feedrate of 5mm/sec. Extracts ~1" OK.
"Mixing as single Right"- No retract, no extrude. Will not print.

After the above test,
1. the 2 motors seem to be operational.
2. the output from Duet board transfers "no functionality" from faulty left side
	to right side extruder.
3. the left extruder skips at 5mm/sec extrusion rate.

I would like your analysis of why the left extruder is non-operational plus steps
	to be taken to rectify.
I would like your explanation as to skipping of the left extruder at 5mm/sec rate.
I would like instructions as to how to remove and re-attach the gray extruded fan
cover on sides and front of extruder. (I would like to be able to see if/when any
motor gear jam takes place.)

Regards,"

************************
Michael, I am hoping that you can spur at least a response from M3D Support.
Regards,
Ron

ftcros, 2019-10-23:
When I was first setting the Promega up I frequently had lag after issuing a command. I then got a screen popup indicating 'connection lost - wait for re-connection' meaning the network IP had lost its connection with the printer. I'm still trying to resolve this problem and have tried a 'static' ip with and without MAC code (\sys\M540 in machine_access.g)

M540 PBE:EF:DE:AD:FE:ED     ; Set MAC address, this can be used to assign a given IP in the DHCP
M552 P0.0.0.0 S1             ; Use this to enable DHCP
; M552 P192.168.1.122 S1        ; Set Static IP address and enable networking

(; M552 P192.168.1.122 is the IP assigned by my DHCP so I incorporated it in the static IP - but still have times when 'connection lost' appears). At present I'm using DHCP with MAC address but I'm also considering using a USB/RJ45 3.0 adapter to connect the printer directly to my PC.

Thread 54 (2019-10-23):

M3D Promega Print bed unstable

ftcros, 2019-10-23:
I am (1) unable to mesh the print bed with results better than very poor (a lot of red on the graph).  I'm using what was shipped with the printer. My print bed is a green, thin 'fiberglass' like material. Should I have a glass print bed?

michaelarmani, 2019-10-23:
The green sheet is an "unbound" print surface made by us.  This is the preferred material and what we use in the factory.  Others have found that buying a very thick marble or glass sheet at their local store is a little more flat.  We also sell a medium thickness glass sheet.  "A lot of red" doesn't mean anything itself as you may just have the bed probe offset set wrong.  what matters is the range and RMS deviations.

ftcros, 2019-10-24:
Thanks, once I applied enough Elmers Glue I began to get results.
The 'red' has become less of concern after I released and then reapplied the bed clips. The bed was brand new when I first secured it in place and began to bulge when heated - now it's more 'seasoned' and lays flatter. Thanks

Closed 2019-10-24.

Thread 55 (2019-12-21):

promega quad

jahreach, 2019-12-21:
there is no promega quad cura profile

michaelarmani, 2019-12-21:
There is a base SD structure for the Mega Quad here:
https://github.com/PrintM3D/Promega/tree/devel/SD%20Card%20Structure/Quad

Building off of that, since Cura has no native quad mixing support, all quad/crane quad/mega quad users need to customize their open source applications to work with their system. For individual color swaps, you can teach Cura to treat each port as a different extruder.  Use the promega compound profile as a starting point.  Also look at the community mods https://coda.io/d/M3D-Official-Troubleshooting-Self-Help-Guide_dzE73kMbIAL/ such as the color mixing post-processor made by sindarius

Closed 2019-12-21.

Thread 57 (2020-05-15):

Adding BLTouch to the ProMega

bluegrassbandit42, 2020-05-15:
Hello,

I am interested in adding a BLTouch to assist with a more level printing situation.

How do I add a BLTouch to this printer?

Thank you,
Alvin J. Holbrook, Jr.
SFC/E-7 (Ret.)
Military Intelligence
US Army

watstogo, 2020-07-10:
Hi there - this document may help [BLTouch on Crane Quad](https://lookaside.fbsbx.com/file/Installing%20a%20BLTouch%20on%20the%20M3D%20Crane%20Quad%20v2.pdf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). For a Promega, you would need to add BLTouch as a Zprobe replacement, so editing some of the sys files outlined in the document aren’t necessary. However, I am having issues with a G28 error (probe not deploying) on Promega with a BLTouch, so I’m trying to figure out why. I’ll post an update if/when I figure it out ;)

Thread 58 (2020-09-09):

Machine keeps crashing when probing G30.

Brian81074, 2020-09-09:
This printer has been nothing but issues from day 1.  Now a year later and 0 successful prints I am giving my final attempt before trashing it.  I have 3 other CR-15 and have no issues with them.  The Promega Compound though I can't even get through the setup.  I get as far as the Z-probe.  I follow the instructions when I engage it and send the G30 command the bed move up until t
[M3d Promega.zip](https://github.com/PrintM3D/Promega/files/5192318/M3d.Promega.zip)
he switch is triggered then the bed crashes to the base and the web interface loses connection for about 15-20 seconds before it comes back up.  I have replaced the z-probe with a part I just purchased from M3D and still the same behavior.  I have a video of the steps and how the printer crashes.
[M3d Promega.zip](https://github.com/PrintM3D/Promega/files/5192319/M3d.Promega.zip)

MendozaDOD, 2021-04-22:
Why are you not runing the macros provided for setup (Macros/Printer Setup/_1_Calibrate_Z_Probe.g)?  There is 25 commands before the G30 that get everything setup for finding the extruder height up from Z-Max and then Deploying the probe...  Once you run all 3 macros in there you will be able to at lease print something.  Without running them you will never have the proper Z height values in the configuration files.

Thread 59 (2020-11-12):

M3D Promega filament feed produces next to nothing or sqiggles

ftcros, 2020-11-12:
I have not, to date, produced more than one print and it was not what I intended.
I've read a few users are not getting anywhere with filament feed. I've used printhead heating methods and slower rates to no end.
Please feel free to enlighten me, please.

marcel-isler, 2020-11-14:
After spending much time trying to beat the stock setup into submission, I ended up redesigning most of the printer and I'm very happy with how it prints now.  Look on Facebook for the ShadowMega Support Group.

Biothermo, 2020-11-25:
I've struggled too with the default configuration. I've had some success, but recently there have been problems with insufficient filament creating a lot of voids.  I noticed a lot of popping noise from the printer head when the problems are worse.  Following these [suggestions ](https://3dprinterly.com/8-ways-how-to-fix-a-clicking-slipping-extruder-on-a-3d-printer/)helped, but didn't solve the problem. Next I disassembled the head and found the [Single K'tana Plastic Insert ](https://promega.printm3d.com/documentation/mechanical-systems/single-ktana)to be badly worn.  This is a 3D printed part which I have [downloaded](https://promega.printm3d.com/printed-parts-bin/bin/extruder-system), but not yet printed.

This is a high-wear point, not suitable for the soft plastic that was provided.  Now I'm wondering what would be the best replacement.

Good luck, Biothermo

ftcros, 2020-11-25:
By no means perfect but the original print head produced for the first time. Had I not found a slicer program, https://slic3r.org/, and slewed the print rate back 50%, it might never have happened.

Reply to ftcros@ftcrosby.com

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

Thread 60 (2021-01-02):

Upgrade to QuadFusion

ChaosRift, 2021-01-02:
Information is still light on this. The upgrade doc looks like a work in progress though.

I cannot find links to the Printed parts needed, like the Quad Adapter mentioned. Where do the bearings come from?

I'm also assuming I need to order the Duet 2, breakout and wiring harnesses.

Do you have a complete list of parts and printed diagrams needed to upgrade to the Quad?

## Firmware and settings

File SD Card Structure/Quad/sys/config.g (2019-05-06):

; CONFIGURATION FILE for Duet Maestro
; Quad Nozzle
; Last modified April 15, 2019

; Executed by the firmware on start-up

; Headers within parenthesis are headings in Duet3D documentation=https://duet3d.com/wiki/Configuring_RepRapFirmware_for_a_Cartesian_printer
; Visit https://reprap.org/wiki/G-code for an explanation of G-code commands

; --- SECTION: GENERAL PREFERENCES ( ) ---

M564 S1 H1									; Enables Homing Requirement For Motor Activation and set axes limits

; --- SECTION: Z-PROBE & MESH COMPENSATION ---

M98 Pmachine_zprobe.g						; configure the z probe

M98 Pmachine_bedmesh.g						; configure the bed mesh

G29 S1										; Load heightmap after power cycle

; --- SECTION: DRIVES (MOVEMENT SECTION) & ENDSTOPS ---

M667 S1										; Enable coreXY mode
M569 P0 S0 D3 V0							; Drive 0 goes backwards, CoreXY_1, stealth chop, disable spread cycle
M569 P1 S1 D3 V0							; Drive 1 goes forwards, CoreXY_2, stealth chop, disable spread cycle
M569 P2 S1 D3 V0							; Drive 2 goes forwards, Z Motor, stealth chop, disable spread cycle

M569 P3 S1 D3 V0                ; Drive 3 (E0)
M569 P4 S1 D3 V0			 			  	; Drive 4 (E1)
M569 P5 S1 D3 V0			 			  	; Drive 5 (E2)
M569 P6 S1 D3 V0			 			  	; Drive 6 (E3)

M98 Pmachine_endstoptypes.g					; set endstop types
M98 Pmachine_steppercurrent.g				; set stepper currents
M98 Pmachine_stepperspeed.g					; set stepper speeds
M98 Pmachine_axisdimension.g				; configure the axes dimensions
M98 Pmachine_axissteps.g					  ; configure the axes steps per mm
M98 Pmachine_extruderstep.g					; configure the extruder steps
G21											; Work in millimetres
G90											; Set to absolute coordinates...
M84 S1										; Set idle timeout

; --- SECTION: HEATERS, BED & THERMISTOR ---
; H0 is bed
; H1 is extruder heater

M570 H0 P25 T30								; Allow heater to be off by as much as 30C for 25 seconds
M570 H1 P15 T30								; Allow heater to be off by as much as 30C for 15 seconds
M305 P0 T100000 B4138 C0 R2200				; Set thermistor + ADC parameters for heater 0, For heated Bed thermistor
M305 P1 T100000 B5140 C1.890000e-7			; Thermistor Config for NTC 100k
M307 H0 A78.9 C265.2 D9.5 S1.00 V24.0 B0	; Forcing heated bed PID control after power-cycle. Basic bed heating auto-tune
M302 P1										; Allow Cold extrudes
M98 Pmachine_maxtemp.g						; set bed and extruder max temperatures

; --- SECTION: FANS ( ) ---

M106 P0 T45 H1 F50                			; Set Heatsink Fan F0 to Thermostatic
M106 P1 H-1 F50                   			; Set Part Cooler Fans F1 to Gcode Control
M106 P2 S0 I0 F4 H-1 L0.3					; Filter fan. Set fan 0 value, PWM signal inversion and frequency. Thermostatic control is turned off, Minimum fan value 0.3, Speed 100%


; --- SECTION: TOOLS ( ) --- 

; Comment: Remember! H0 is the heated bed!
; Comment: D0 is the first driver after movement (X, Y and Z) drives, which are the extruders

M98 Pmachine_quad_tools.g				; Define quad tools

T0											; Automatic tool select

; --- SECTION: NETWORKS (PROLOGUE & COMMUNCATIONS SECTION) ---
M98 Pmachine_access.g						; set machine name and IP
M586 P0 S1									; Enable HTTP
M586 P1 S0									; Disable FTP
M586 P2 S0									; Disable Telnet

; --- SECTION: MISCELLANEOUS --- 

;M98 Pqc.g									; Do NOT uncomment unless you really know what you're doing

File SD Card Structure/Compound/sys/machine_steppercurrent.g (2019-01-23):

; machine_steppercurrent.g
; October 1, 2018

; This document sets the stepper motor currents.
; This is an advanced feature and should only be changed if you REALLY know what you're doing!
; Increasing stepper motor currents beyond their limit can result in damage to them!

M906 X680 Y680 Z600 E400 I60; Set motor currents (mA) and idle current percentage

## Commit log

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2018-07-18 Added Endstop type configuration
    This checkin adds machine_endstoptypes.g as well as the startcode.g and stopcode.g files which can be called from within the slicer to do nozzle priming etc.
    Cleaned up some discrepancies between the Compound and K'Tana structures
    [bed.g, config.g, deployprobe.g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]
2018-07-18 Added Endstop Types configuration (Part 2)
    Not sure why this file didn't go with the other check in
2018-07-18 Renamed start and stop code
    To keep the two start and stop code files together, I changed the naming convention to:
    print_startcode.g
    print_stopcode.g
    [print_startgcode.g, print_stopgcode.g]
2018-07-19 Moved Micro stepping into machine files
    The micro step configuration for axis and extruders have been moved into their corresponding machine files.
    Also changed the extruder micro stepping to 128 to improve precision of low percentage mixing on short line elements
    [config.g, machine_axissteps.g, machine_extruderstep.g]
2018-07-21 Updated K'Tana config to match Compound
    This moves the microstepping configuration into machine_axissteps.g and machine_extruderstep.g
    [config.g, machine_axissteps.g, machine_extruderstep.g]
2018-07-21 Changed heater back to H1
    A lot of people had issues that the heater got switched to H2 which does not seem to reflect the configuration of the machines being delivered.
    [machine_compound_tools.g]
2018-07-21 Revert "Changed heater back to H1"
    This reverts commit d2bcc4c63ca79af5bd30b23b4cc57db145200d5a.
    [machine_compound_tools.g]
2018-07-21 Added explanation on 2000C issue
    Added additional wording to A Instruction.txt to explain how to deal with the 2000C heater issue.
2018-07-21 Gave HomeZ a bit more distance to properly find the optical endstop
    [homez.g]
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2018-07-25 Added Printer Setup Macros
    Added three macros that simplify printer setup
    Updated the instructions accordingly
    [_1_Calibrate_Z_Probe.g, _2_Set_Z_Endstop_Height.g, _3_Mesh_Bed.g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]
2018-07-26 Setting the Z Probe Distance after homing Z now
    There was an issue where changing the Z Probe Distance would not take until you restart the printer. Now you just have to home the Z axis to set it
    [homez.g]
2018-07-27 Additional macro message output
    Added additional macro messages at the end to record what was communicted to the user in the g-code log.
    [_1_Calibrate_Z_Probe.g, _2_Set_Z_Endstop_Height.g]
2018-07-27 Additional Macro messages
    This file for some reason didn't get commited in the previous one
    [_2_Set_Z_Endstop_Height.g]
2018-07-29 Added config entry for Metrol Z Probe
    This added a config line for the Metrol Z Probe.
    The X and Y offset need to be measured after installing the probe!
    [machine_zprobe.g]
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2018-08-17 ProMega Machine Profile for Cura
    This profile contains settings for both Compound as well as K'Tana extruders
    [CFDMP_Promega_Machines.curaproject.3mf]
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2018-08-22 Update to extruder steps
    K'Tana extruder micro stepping set back to 16
    Compound extrusion set to 200.4 to adjust for 128 microstepping
    [machine_extruderstep.g]
2018-08-31 Added a revised version from TheBum
    This version fits when using Talryyn's Belt Shoes
    [Optical_Z_Endstop_Holder_-_Rev_A.stl]
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2018-09-04 New version of the Fan Shroud that now fits under the front edge
    Made slight changes to the fan shroud so that it can now fit under the front metal edge.
    Read the ReadMe.txt!
    [ProMega Front Fan Shroud With Top Fin v21.f3d, ProMega Front Fan Shroud With Top Fin v21.iges, ProMega Front Fan Shroud With Top Fin v21.step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]
2018-09-04 Reduce Stepper Power during homing
    Stepper power is reduced to 60% during the homing process to be more gentle on the limit switches.
    [homex.g, homez.g]
2018-09-11 Added new macro to test the four corners
    This macro tests the four corners to see if you're aproximately leveled
    [_0_Check_Corners.g]
2019-01-02 Promega-Quad version addition
    This addition is preliminary. Confirmation is pending after guides are made.
    [_1_Calibrate_Z_Probe.g, _2_Set_Z_Endstop_Height.g, _3_Mesh_Bed.g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]
2019-01-18 Update config.g
    Corrects motor direction and modes (always spreadcycle)
    Changes heater sensor to thermistor
    Sets fan settings, similar to crane quad
    Additional minor clean up
    [config.g]
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2019-01-18 Update machine_quad_tools.g
    Update extruder driver modes (always spreadcycle)
    Update fan configuration, mimic crane quad
    Update e steps
    [machine_quad_tools.g]
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2019-03-19 Update _1_Calibrate_Z_Probe.g
    The Promega Quad mount has a different Z Probe than the default print heads. This Macro should have already been updated to reflect this!
    The changes include:
    1> Lowering the bed to 100mm Z axis instead of 20mm so there is room for actual hands to get in there and pull the z probe out and put it into the other slot.
    2> Since the bed was lowered to 100mm, it should be raised to 20mm quickly before probing is started so that probing doesn't take a lot longer than necessary. This could easily be 10mm instead of 20. I just put it back to 20mm because that is where the other macros for the other heads start from, so this makes it consistent with them.
    3> I sl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
    [_1_Calibrate_Z_Probe.g]
2019-03-19 Update _3_Mesh_Bed.g
    This setup macro also should have already been edited like this to allow room for the z probe to be deployed when using the Promega Quad Mount. The Promega Quad Mount requires a LOT more room for you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
    This line: "G1 Z20 F1500 ;" might need to be removed (I don't remember right now if the beginning of the bed mesh starts by homing the axis... if it does home the axis then there is no need to raise 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
    [_3_Mesh_Bed.g]
2019-03-30 Update bed.g - Remove ferences to T1 and T2
    There is no such tool as T1 and T2 in the Quad. It is clear that M3D copied the configs for the quad from one of the other heads and failed to test it. If they had tested it, at all, then these issues could have easily been fixed by someone that is supposed to be familiar with this code. Instead, 3+ months after the Quad head was shipping to ProMega backers, I have had to find and fix these errors while I'm trying to just get my printer to work properly for the first time. I have spent several days worth of hours just trying to get my first print to work properly and have spent so much of that time just fixing things that M3D has failed to del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
    [bed.g]
2019-03-30 Update _1_Calibrate_Z_Probe.g
    Under ";turn on extruder" section, remove the calls containing P1 and P2. From what I understand from user DroneOn, the P1 and P2 actually refer to Tool 1 and Tool 2.... not really extruders. The quad only has one tool: T0, so P0 is what should be turned on.
    Credit for this fix goes to DroneOn. I'm just submitting it for everyone else to benefit from it.
    [_1_Calibrate_Z_Probe.g]
2019-03-30 Update _2_Set_Z_Endstop_Height.g
    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
    [_2_Set_Z_Endstop_Height.g]
2019-03-30 Update _3_Mesh_Bed.g
    Same thing as the other two setup macros: Need to remove the call to P1 and P2 because those actually refer to Tool 1 and Tool 2 which don't exist for the Quad. Credit goes to user DroneOn for pointing out this fix. I'm just sharing it with everyone. M3D: You really should have found and fixed these problems in December / January. The fact that the most basic errors are present unfixed 3+ months later really tells me you don't care about supporting people that have supported you. This tells me that you haven't actually followed your own instructions and used your own setup materials to properly setup a Quad Fusion ProMega Build yet. If you had, these problems wou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
    [_3_Mesh_Bed.g]
2019-03-30 Update config.g
    I believe this config file was copied over from a different extruder. For the Quad, there is only 1 extruder heater. So H2 is nonsense and should be removed. I also noticed that in the original file, there was only one line for M143 H1 S265 ; Set temperature limit for heater 1 to 265C. If there really was a second heater, then why wouldn't H2 also have that limit set?
    It is my observation that all of these files need to be CAREFULLY reviewed by M3D for errors. So far I have found many errors. It appears that the quad configuration was copied from a different head and not all the changes were made that were necessary to make it work right, to remove errors, and to re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
    [config.g]
2019-03-31 Update machine_extruderstep.g
    The extruder steps that were in this file were obviously not anywhere close to correct for the Quad. Yet another copy and paste error by M3D that they haven't caught because they haven't tested what they are putting out there for 3+ months. So sad.
    [machine_extruderstep.g]
2019-03-31 Update config.g
    Fixing comment on Drive 0 goes backwards (not forwards). Also adding D3 to those 3 lines to force Spreadcycle mode all the time so there is no layer shifting caused by the crossover from Stealthchop over to Spreadcycle. (Thanks DroneOn for explaining this to me and for the fix itself. I'm merely posting it. Credit goes to him.)
    [config.g]
2019-03-31 Update machine_corexy_motions_settings.g
    Credit goes to DroneOn. He was explaining to me that these settings as they were written before were incomplete and that these are closer to what is needed here. Makes sense to me seeing the obvious dual extruder portion of the line that shouldn't even be there for the Quad...or if it should, it should have 4 ratios, not 1 ratio. I believe the single value to be correct and is what I'm using now.
    [machine_corexy_motion_settings.g]
2019-04-14 Update bed.g
    Removed spurious code used when user switches back and forth between different head configurations. But there is no T2 to invoke in this context.
    [bed.g]
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2019-04-15 PromegaQ update
    uploading local, modified version
    Summary changes:
    config setup redefinition (derived from regular Promega)
    added applicable craneQ configurations
    [_1_Calibrate_Z_Probe.g, _2_Set_Z_Endstop_Height.g, _3_Mesh_Bed.g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]
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2019-04-15 Update machine_axissteps.g
    Resetting initial microstepping for x y and z axises
    [machine_axissteps.g]
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2019-04-15 Update machine_axissteps.g
    Switching initial micro-stepping to 16, for x y z axes
    [machine_axissteps.g]
2019-04-16 Community Macros Update
    Updated wording of messages.
    Minor movement changes.
    Updated format of saved instruction messages (displayed on gcode console)
    [_1_Calibrate_Z_Probe.g, _2_Set_Z_Endstop_Height.g, _3_Mesh_Bed.g]
2019-04-22 Added blank heightmap.csv
    Added to avoid having heightmap not found errror (for initial setups).
    (All values in blank heightmap are 0.)
    [heightmap.csv]
2019-04-22 Community Macros Update
    Improved wording of the messages/displays shown throughout the macros.
    Minor functionality change to _3_Mesh_Bed. User will have option to turn off bed/extruder (as oppose to saying a reminder, in the display)
    All changes applied to both K'Tana & Compound
    [_1_Calibrate_Z_Probe.g, _2_Set_Z_Endstop_Height.g, _3_Mesh_Bed.g]
2019-05-04 Update confiig.g - Fixing comment
    The direction of P0 is different from P1 and P2, so I can see there is an error in the comment. Looking up that Mcode, it says that S0 is backwards and S1 is forwards.
    [config.g]
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2019-05-04 Update config.g - Extruder Motor Direction
    The extruder stepper motor direction is wrong. You guys removed a large block out of machine_quad_tools.g and then put the wrong motor direction into config.g. If this mistake was "live" for a day or two and one of you guys eventually found it, that would be one thing.
    This mistake has been up for 18 days and it is clear to me that after you guys make massive changes to the SD Card Sturcture that no one there is actually taking the time to download the files that you expect your customers to use and at least trying them out to make sure they work. This is simple QC work. You should have someone working for you that checks for basic func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
    [config.g]
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
